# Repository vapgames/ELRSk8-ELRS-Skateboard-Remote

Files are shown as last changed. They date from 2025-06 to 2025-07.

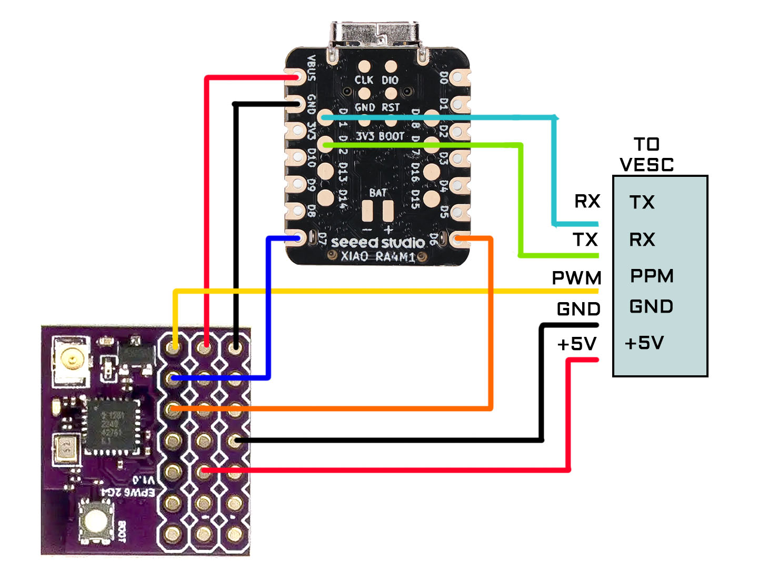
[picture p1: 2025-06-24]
schematicReceiver1.jpg

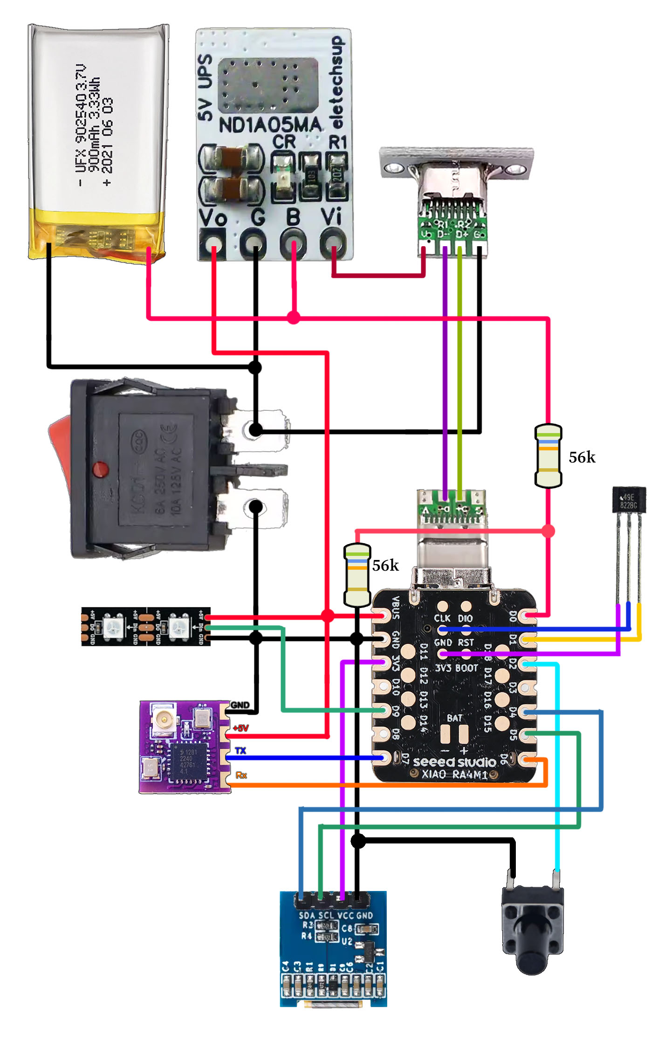
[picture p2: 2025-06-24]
schematic1.jpg

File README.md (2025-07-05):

# ELRSk8
combinedPhoto1

**This readme is under construction, more instructions and schematics are coming!**

ELRSk8 is an open source remote for DIY electric skateboard utilizing the power of [ExpressLRS](https://github.com/ExpressLRS), running on arduino-compatible controllers.

Main features I tried to achieve with this project:

1. Solve the connection and safety issue with off the shelf remotes. Low latency connection, better than NRF or BLE protocols. ELRS seems like the best open source link right now with superior interference and failsafe handling.
2. Durable throttle control with bearings, high reliability sensor and tension adjustment.
3. Ergonomic grip for use with wrist guards and gloves.
4. Basic telemetry
5. Easily sourced components, arduino compatible boards, 3d printed shell.

Code is based on ELRS control implementation from [Simple TX](https://github.com/kkbin505/Arduino-Transmitter-for-ELRS) by @kkbin505 and [AlfredoCRSF](https://github.com/AlfredoSystems/AlfredoCRSF) library by @AlfredoSystems

I've been iterating on this system for over 1 year, and I've been riding using this remote for 6 months. And at this point I'm confident enough in this design to share it.

# Remote:
<details> <summary>Remote parts you'll need (Click to expand)</summary>
  
- ExpressLRS (ELRS) - Currently it is the most reliable opensource link protocol with great interference and failsafe handling. ELRS receivers can be configured as transmitters, and there's a huge selection of different models. You can use any esp8285 based receiver for TX, I recommend "Happymodel ep1 TCXO" as TX and "Happymodel EPW6 TCXO" as RX.
  


- controller: RA4M1 it's compact and setup is straightforward. Alternatively you can use STM32F103C8T6 Blue pill (but you need to flash bootloader and remove pins to make it fit). [Xiao RA4M1](https://wiki.seeedstudio.com/getting_started_xiao_ra4m1/) OR [Waveshare RA4M1](https://www.waveshare.com/wiki/RA4M1-Zero)


- Sensor: SS49E or A1324 linear hall sensor.
  

 
- Neodimium magnets 5x3

- Bearings: MR128 ZZ (or MR128 RS)  8 * 12 * 3.5mm
  


- Spring from Bic lighter.

- Battery: 802540 or 902540 900mah li-ion spicy pillow (lasts >6 hours, haven't tested beyond that)



- Usb C port: generic pcb soldered 4 pin port.
  


- 6x6x7 button for telemetry menu
  


- Power switch: KCD1-110
  


- OLED 0.49" i2c 64x32
  


- Power supply:

    - 5v UPS module ND1A05MA - combines 0.5A charging and discharging, but seems like it's not very widely available
      
    

     - alternatively you can use 2 separate modules for charging and discharging. Look for 500ma small capacity charging module + 5v boost module
       
     

- 56k resistors x 2. For battery voltage measurement.

- Shell printed with PETG (or any other low friction material). Grips printed with TPU95a.
 
- Hardware 
  - set of m2 screws 6-12mm
    
  - m5x4 or m5x5 set screw (same as in HTD5m pulley)
    
    

- Optional WS2812 LEDs
</details>

Remote schematic for XIAO RA4M1 and ND1A05MA
schematic1



# Receiver:
- Any ELRS receiver will do. But if you want to have telemetry at this point you'll need a PWM receiver. I use Happymodel EPW6, it can do UART and PWM at the same time.

- For telemetry - to talk to VESC you need RA4M1 / STM32F103C8T6 . Or any other arduino-compatible controller that can do **2 UARTS!**

schematicReceiver1

---
# ELRS Flashing and configuring
- <details> <summary>How to enter ELRS WIFI mode (Click to expand)</summary>
  
  * For me ELRS WIFI doesn't work on my laptop, but it works on my phone.
  
  * By default ELRS receiver/transmitter will go into WIFI mode 60 seconds after power up, if there's no connection.
  
  * For fresh receiver you can power it with GND and +5v and wait 60 seconds.
  
  * If connection was established between remote and the board receiver, it will not go into WIFI mode until power cycle. So to connect WIFI to your board - keep remote turned off, power the board on, wait 60 seconds.

  * For soldered remote, the TX module will not go into WIFI mode while it's receiving packets from arduino controller. To go into WIFI mode you need to flash empty sketch (like a blinker sketch) onto the remote, then wait 60 seconds.
  
  * Choose WIFI named ExpressLRS RX (or TX). Press "Use network as is":
    
     

  * After this you can go into a browser and type address 10.0.0.1
  Here you can set your Bind Phrase, tweak pin settings, and upload the firmware (that you download from [web flasher](https://expresslrs.github.io/web-flasher/))

     
</details>

- <details> <summary>How to flash Ep1 as TX (Click to expand)</summary>
  
  * Go to https://expresslrs.github.io/web-flasher/
  
  * Choose Receiver:
  
    

  * Choose latest ELRS and these receiver settings:
  
    

  * Set your bind phrase, go to Advanced Settings and check "Flash RX as TX"
  
    

  * Download firmware and flash using WIFI method OR serial FTDI adapter
  
</details>

- <details> <summary>How to configure EPW6 for PPM and UART telemetry (Click to expand)</summary>
  
  * Go into receiver WIFI mode
    
  * CH1 is throttle PWM, I've increased mine to 100HZ, test this for your particular VESC. Make sure to setup **failsafe pos to 1500**.
    
  * CH2 and CH3 should be Serial TX and RX.
  
    

</details>

- <details> <summary>How to flash with FTDI adapter (Click to expand)</summary>
  
  * The "I wasn't asking" method that I prefer over WIFI flashing.
  
  * Bridge the boot pin or press the boot button before powering up before flashing.
  
    FTDIFlashing1

  * Use flashing method "Serial UART"
  
    

  * Select your FTDI serial in popup

    

</details>

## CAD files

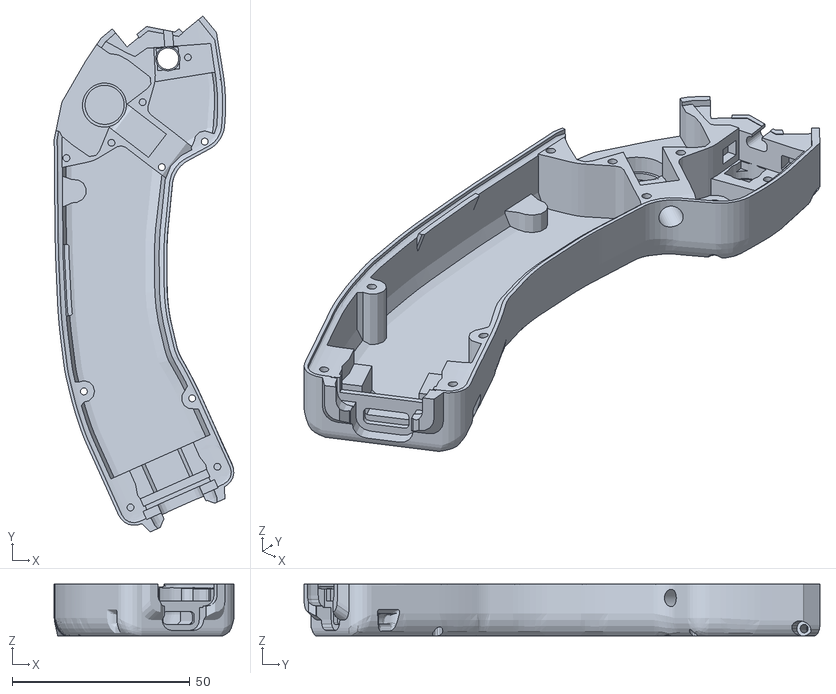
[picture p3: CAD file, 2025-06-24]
STL/remoteShellBottom.stl
50.5 x 145.0 x 14.6

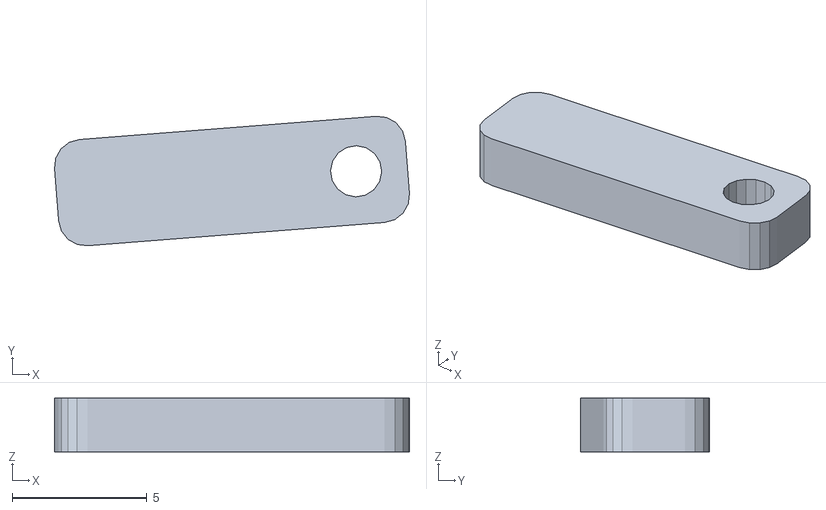
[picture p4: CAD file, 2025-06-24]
STL/buttonHolder.stl
13.2 x 4.80 x 2.00

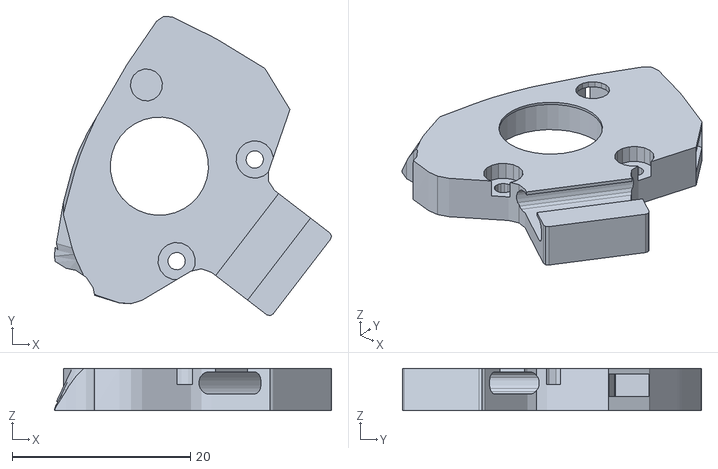
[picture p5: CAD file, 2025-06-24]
STL/gimbalLid.stl
31.0 x 33.6 x 4.71

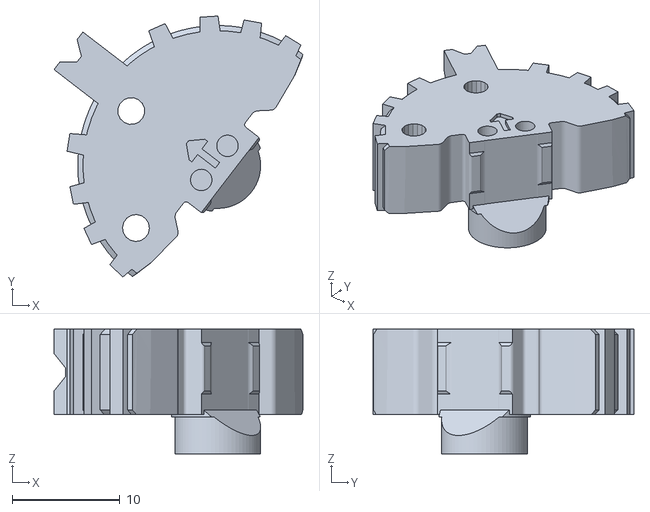
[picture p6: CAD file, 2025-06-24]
STL/knob.stl
23.1 x 24.2 x 11.6

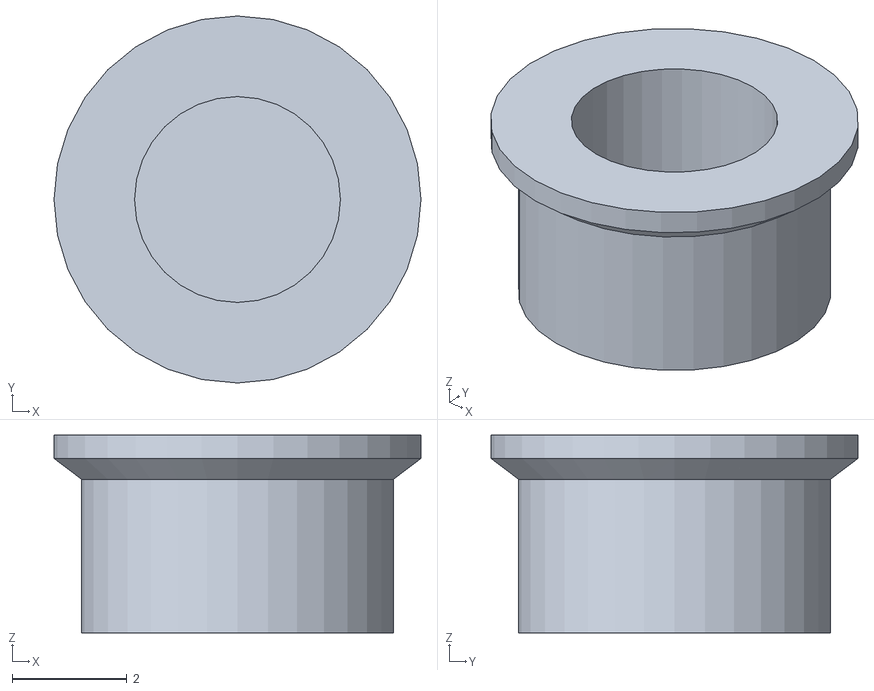
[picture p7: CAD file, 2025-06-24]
STL/buttonCap.stl
6.40 x 6.40 x 3.45

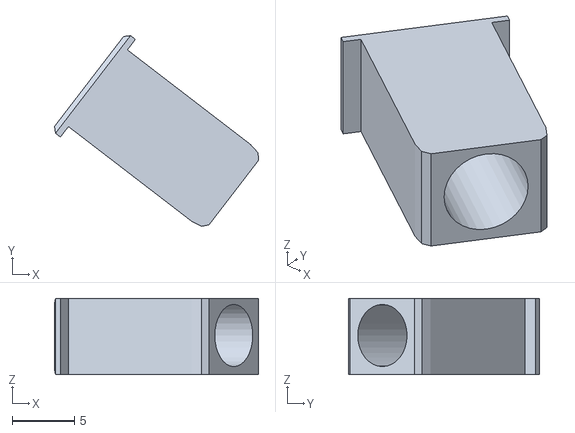
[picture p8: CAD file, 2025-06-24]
STL/plunger.stl
16.4 x 15.3 x 6.14

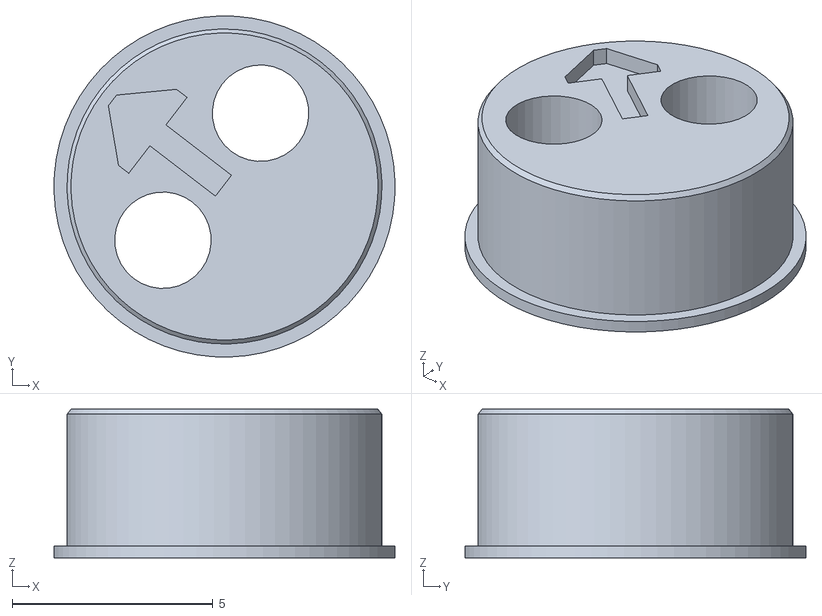
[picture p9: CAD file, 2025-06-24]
STL/axle.stl
8.49 x 8.49 x 3.70

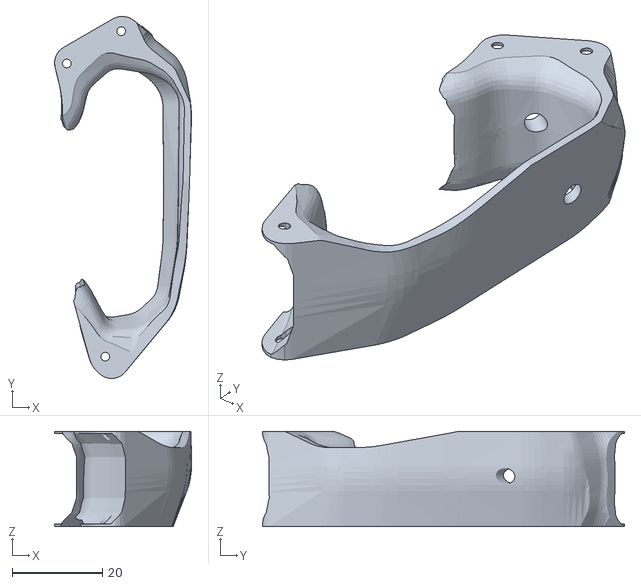
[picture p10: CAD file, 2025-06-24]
STL/grip.stl
30.4 x 80.3 x 21.2

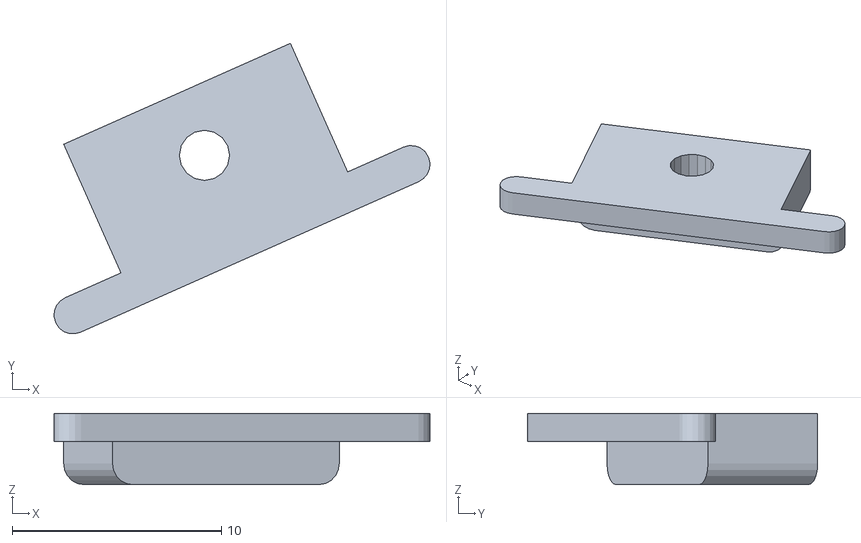
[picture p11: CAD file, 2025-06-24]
STL/usbPlug.stl
18.0 x 13.9 x 3.40

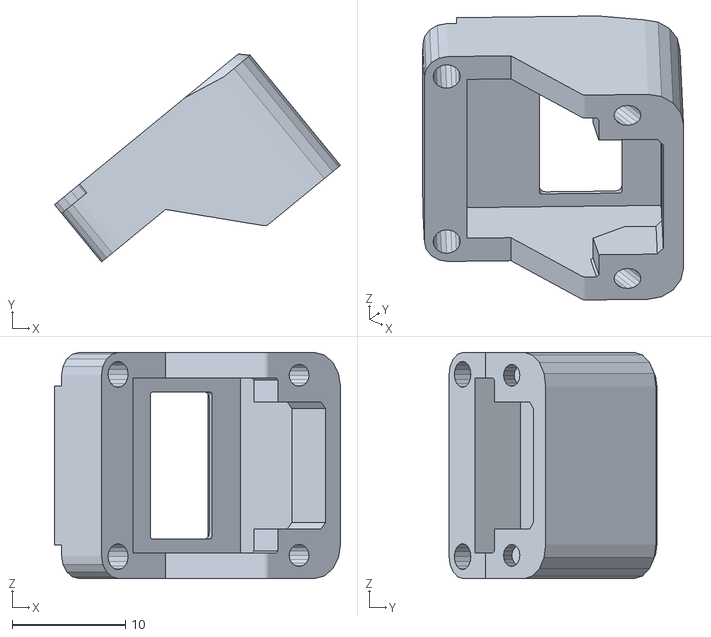
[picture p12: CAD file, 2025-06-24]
STL/oledCase.stl
25.3 x 18.4 x 20.0

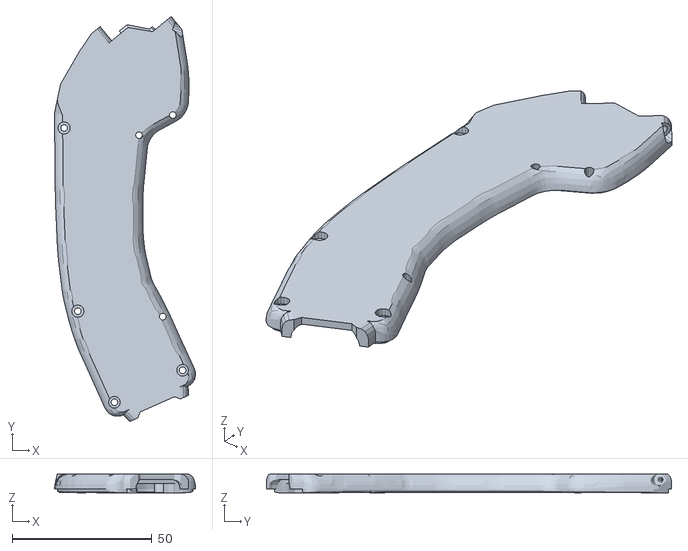
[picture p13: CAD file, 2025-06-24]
STL/remoteShellTop.stl
50.5 x 145.0 x 6.79

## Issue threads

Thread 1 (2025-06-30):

Parts

beadon, 2025-06-30:
Looking at the pictures closely, I think there are 2 (minor) additions worth mentioning in the assembly.

1. Kapton tape covering some of the connectors near the power charging section
2. Fabric(?) tape holding the throttle wires in place on one side of the remote shell.
3. padding material(?) on the inside "top" cover to pressure-mount the battery+MCU.

For someone building it without these items, it seems like the install might be a little frustrating.  Thoughts ?

Also, I think the adhesives in the fabric tape are going to break down in my relatively humid environment, so I am an advocate of some kind of "clip" or other type of cable raceway that does not require this.

beadon, 2025-07-07:
yes, that would be great.   Other people will have the same questions, I am just trying to make things easier for them.  :)

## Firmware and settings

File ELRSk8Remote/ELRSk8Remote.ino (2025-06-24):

#include <Arduino.h>
#include "crsf.h"
#include "led.h"
#include "oledScreen.h"

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
//REQUIRED LIBRARIES:
//U8x8lib
//Adafruit_NeoPixel

//CONFIG////////////////////////////

//#define CALIBRATION

//#define STM32F103C8
#define XIAOR4M1

//PINS
#ifdef STM32F103C8
  //board: generic stm32f1
  //bluepillf103c8
  //USART support: enabled (generic serial)
  //USB: CDC generic serial
  //upload method: hid bootloader 2.2
  #define CRSF_RX PB11
  #define CRSF_TX PB10
  #define OLED_SDA PB7
  #define OLED_SCL PB6
  #define VOLTAGE_READ_PIN PA6
  #define THROTTLE_PIN PA4
  #define MENU_BUTTON1_PIN PB4
  #define RGBLED_PIN PA8
  HardwareSerial CRSFSerial(CRSF_RX, CRSF_TX);
  #define CRSF_SERIAL_BAUDRATE  400000
  #define ADCResolution 12
 
  int throttleLow = 670;
  int throttleMid = 2165;
  int throttleHigh = 3650;
  
  float batteryRealVoltageLow = 3.84f;
  float batteryRealVoltageHigh = 4.2f;
  float batteryADCLow = 2341.0f;
  float batteryADCHigh = 2540.0f;
#endif

#ifdef XIAOR4M1
  #define CRSF_RX D7
  #define CRSF_TX D6
  #define OLED_SDA D4
  #define OLED_SCL D5
  #define VOLTAGE_READ_PIN A0
  #define THROTTLE_PIN A1
  #define MENU_BUTTON1_PIN A2
  #define RGBLED_PIN D9
  #define CRSFSerial Serial1
  #define CRSF_SERIAL_BAUDRATE  400000
  #define ADCResolution 14
  
  int throttleLow = 4950;
  int throttleMid = 8320;
  int throttleHigh = 11650;

  float batteryRealVoltageLow = 3.82f;
  float batteryRealVoltageHigh = 4.2f;
  float batteryADCLow = 9780.0f;
  float batteryADCHigh = 10460.0f;
#endif

int throttleSamples = 1;    //YOU CAN TRY MULTISAMPLING FOR THROTTLE INPUT IF YOU THINK IT'S TOO NOISY

int ELRSpacketRate = 3;     // 0 - 50Hz / 1 - 100Hz Full / 2- 150Hz / 3 - 250Hz / 4 - 333Hz Full / 5 - 500Hz
int ELRSpower = 0;          // 0 - 10mW / 1 - 25mW / 2 - 50mW /3 - 100mW
int ELRStelemetryRate = 4;  // 0 - Std / 1 - Off / 2 - 1:128 / 3 - 1:64 / 4 - 1:32 / 5 - 1:16 / 6 - 1:8 / 7 - 1:4 / 8 - 1:2 / 9 - Race

#define KILOMETERS
//#define MILES

//END CONFIG////////////////////////


CRSF crsf;
uint8_t crsfPacket[CRSF_PACKET_SIZE];
uint8_t crsfCmdPacket[CRSF_CMD_PACKET_SIZE];
int16_t rcChannels[CRSF_MAX_CHANNEL];
unsigned long crsfTime = 0;
unsigned long loopCount = 0;
unsigned long currentMillis = 0;
float throttle = 0;
float remoteBatteryPercent = 0;
float animationTime = 0;
OledScreenMenu oledScreen;

void setup()
{
  analogReadResolution(ADCResolution);
  pinMode(LED_BUILTIN, OUTPUT);
  pinMode(VOLTAGE_READ_PIN, INPUT);
  //TURN OFF LED TO SAVE POWER
  digitalWrite(LED_BUILTIN, HIGH); //INVERTED ON STM32f103
  
  //OLED
  int screenMode = SCREEN_VOLTAGE_DISTANCE;
  bool useKilometers = true;
  #ifdef CALIBRATION
    screenMode = SCREEN_CALIBRATION;
  #endif
  #ifdef MILES
    useKilometers = false;
  #endif
  
  oledScreen.Setup(MENU_BUTTON1_PIN, screenMode, useKilometers);
  
  //DRAW SCREEN
  for (uint8_t i = 0; i < screenTextWidth * screenTextHeight; i++) {
    oledScreen.Update();
  }

  //LED
  SetupLED(RGBLED_PIN);

  //CRSF
  //SET CHANNELS
  for (uint8_t i = 0; i < CRSF_MAX_CHANNEL; i++) {
      rcChannels[i] = (CRSF_DIGITAL_CHANNEL_MIN + CRSF_DIGITAL_CHANNEL_MAX) / 2;
  }
  //START CRSF
  delay(100);
  CRSFSerial.begin(CRSF_SERIAL_BAUDRATE);
  crsf.begin(CRSFSerial);
  crsfTime = micros();
  
  //DEBUG
  Serial.begin(115200);
  
  #ifdef CALIBRATION
    throttleMid = SampleThrottle(100);
    throttleLow = throttleMid;
    throttleHigh = throttleMid;
  #endif
}

float SampleThrottle(int samples) {
  float potInput = 0;
  for(int i = 0;i < samples;++i) {
  potInput += (float)analogRead(THROTTLE_PIN);
  }
  potInput /= samples;
  return potInput;
}

float mapfloat(float x, float in_min, float in_max, float out_min, float out_max)
{
  return constrain((x - in_min) / (in_max - in_min), 0.0f, 1.0f) * (out_max - out_min) + out_min;
}

float mapfloatUnclamped(float x, float in_min, float in_max, float out_min, float out_max)
{
  return (x - in_min) / (in_max - in_min) * (out_max - out_min) + out_min;
}

float lerp(float a, float b, float x)
{ 
  return a + x * (b - a);
}

float clamp(float x, float xMin, float xMax)
{ 
  if(x < xMin) {
    return xMin;
  }
  if(x > xMax) {
    return xMax;
  }
  return x;
}



bool CRSFUpdate() {
  unsigned long currentMicros = micros();
  //INPUT+CRSF - 635us
  if (currentMicros - crsfTime > CRSF_TIME_BETWEEN_FRAMES_US) {
    //Serial.println(currentMicros - crsfTime); //PERFORMANCE CHECK, should be close to 4000 usec
    //THROTTLE INPUT
    float potInput = SampleThrottle(throttleSamples);
    
    int CRSFThrottle = CRSFMid;
    if(potInput < throttleMid) {
      CRSFThrottle = round(mapfloat(potInput, throttleLow, throttleMid, CRSFMin, CRSFMid));
    }
    else {
      CRSFThrottle = round(mapfloat(potInput, throttleMid, throttleHigh, CRSFMid, CRSFMax));
    }

    #ifdef CALIBRATION
      rcChannels[AILERON] = CRSFMid; //DO NOT SEND THROTTLE COMMANDS DURING CALIBRATION
    #else
      rcChannels[AILERON] = CRSFThrottle;
    #endif
    
    throttle =  mapfloat(potInput, throttleLow, throttleHigh, -1.0f, 1.0f);
    

    //SEND
    if (loopCount <= 500) {
        //ESTABLISH CONNECTION BY SENDING NORMAL PACKETS
        crsf.crsfPrepareDataPacket(crsfPacket, rcChannels);
        crsf.CrsfWritePacket(crsfPacket, CRSF_PACKET_SIZE);
        loopCount++;
    } else if (loopCount > 500 && loopCount <= 505) {
        crsf.crsfPrepareCmdPacket(crsfCmdPacket, ELRS_PKT_RATE_COMMAND, ELRSpacketRate);
        crsf.CrsfWritePacket(crsfCmdPacket, CRSF_CMD_PACKET_SIZE);
        loopCount++;
    } else if (loopCount > 505 && loopCount <= 510) {
       crsf.crsfPrepareCmdPacket(crsfCmdPacket, ELRS_POWER_COMMAND, ELRSpower);
        crsf.CrsfWritePacket(crsfPacket, CRSF_PACKET_SIZE);
        loopCount++;
    } else if (loopCount > 510 && loopCount <= 515) {
        crsf.crsfPrepareCmdPacket(crsfCmdPacket, ELRS_TLM_RATIO_COMMAND, ELRStelemetryRate);
        crsf.CrsfWritePacket(crsfCmdPacket, CRSF_CMD_PACKET_SIZE);
        loopCount++;
    }
    else {
        //SEND CHANNELS
        crsf.crsfPrepareDataPacket(crsfPacket, rcChannels);
        crsf.CrsfWritePacket(crsfPacket, CRSF_PACKET_SIZE);
    }

    crsfTime = currentMicros;
    return true;
  }
  //Serial.println((micros() - currentMicros));

  return false;
}

void MeasureRemoteBattery() {
  //INTERNAL BATTERY VOLTAGE
  float batteryADC = (float)analogRead(VOLTAGE_READ_PIN);
  float batteryVoltage = mapfloatUnclamped(batteryADC, batteryADCLow, batteryADCHigh, batteryRealVoltageLow, batteryRealVoltageHigh);
  float newPercent = mapfloat(batteryVoltage, 3.2f, 4.2f, 0, 1);
  remoteBatteryPercent = lerp(remoteBatteryPercent, newPercent, 0.1f);
  oledScreen.remoteBatteryPercent = remoteBatteryPercent * 100;
}

void UpdateLed() {

  if(loopCount < 400)
  {
    //BLINK ON START
    LEDColorRGB.r = lerp(255, 0, remoteBatteryPercent);
    LEDColorRGB.g = lerp(0, 255, remoteBatteryPercent);
    LEDColorRGB.b = 0;
    blinkLED(100);
  }
  else {
    if(throttle > - 0.1f) {
      //IDLE FLASH WHITE
      animationTime += 0.01f;
      float anim = clamp(sin(animationTime) * 4 - 3, 0, 1);
      LEDColorRGB.r = lerp(0, 30, anim);
      LEDColorRGB.g = lerp(0, 40, anim);
      LEDColorRGB.b = lerp(0, 30, anim);
      
      LightLed();
    }
    else {
      //BRAKING FLASH RED
      animationTime += (0.005f - 0.015f * throttle) * 4;
      float anim = sin(animationTime) * 0.5f + 0.5f;
      LEDColorRGB.r = lerp(0, 255, anim);
      LEDColorRGB.g = 0;
      LEDColorRGB.b = 0;
      LightLed();
    }
  }

  if(animationTime > 10000.0f) {
    animationTime = 0;
  }
}

unsigned long measureMicros = micros();
int packetsPerSecond = 0;
void loop()
{
    bool crsfUpdated = CRSFUpdate();
    
    if(crsfUpdated)
    {
      ++packetsPerSecond;
      if(micros() - measureMicros > 1000000) {
        //oledScreen.distance = ((float)packetsPerSecond) * 0.1f;
        //Serial.println(packetsPerSecond);
        measureMicros = micros();
        packetsPerSecond = 0;
      }
    }
    
    
    if(!crsfUpdated) {
      //RECEIVE TELEMETRY
      crsf.handleSerialIn();
    }
    else {
      //DO SCREEN UPDATE ONCE AFTER CRSF UPDATE
      MeasureRemoteBattery();
      UpdateLed();

      //SEND TELEMETRY VALUES TO SCREEN
      oledScreen.voltage = ((float)crsf._battery.voltage) * 0.001f;
      oledScreen.distance = ((float)crsf._battery.capacity) * 0.1f;
      oledScreen.speed = ((float)crsf._battery.current) * 0.001f;
      oledScreen.current = ((float)crsf._battery.remaining) * 0.5f;
      
      //oledScreen.linkQuality = crsf._linkStatistics.uplink_Link_quality;
      //oledScreen.rssi = crsf._linkStatistics.uplink_RSSI_1;
      oledScreen.linkQuality = crsf._linkStatistics.downlink_Link_quality;
      oledScreen.rssi = crsf._linkStatistics.downlink_RSSI;
      oledScreen.Update();
    }


    #ifdef CALIBRATION
      int potInput = analogRead(THROTTLE_PIN);
      throttleLow = min(throttleLow, potInput);
      throttleMid = potInput;
      throttleHigh = max(throttleHigh, potInput);
      int calibrateVoltage = analogRead(VOLTAGE_READ_PIN);

      oledScreen.throttleCalibrate = potInput;
      oledScreen.batteryCalibrate = calibrateVoltage;
      
      Serial.println("------------------");
      Serial.print("int throttleLow = ");
      Serial.print(throttleLow);
      Serial.println(";");
      Serial.print("int throttleMid = ");
      Serial.print(throttleMid);
      Serial.println(";");
      Serial.print("int throttleHigh = ");
      Serial.print(throttleHigh);
      Serial.println(";");
      Serial.print("//battery = ");
      Serial.println(calibrateVoltage);
    #endif
}

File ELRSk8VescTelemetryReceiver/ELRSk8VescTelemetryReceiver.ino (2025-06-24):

#include <VescUart.h>
#include <SimpleKalmanFilter.h>
#include <stdio.h>
#include "crsfTelemetry.h"
#include <Arduino.h>

//REQUIRED LIBRARIES:
//VescUart
//AlfredoCRSF
//SimpleKalmanFilter

//CONFIG////////////////////////////

//#define STM32F103C8
#define XIAOR4M1

//PINS
#ifdef STM32F103C8
  #define VESC_RX PB11
  #define VESC_TX PB10
  #define CRSF_RX PA10
  #define CRSF_TX PA9
  
  HardwareSerial VESCSerial(VESC_RX, VESC_TX);
  HardwareSerial CRSFSerial(CRSF_RX, CRSF_TX);
 #endif

#ifdef XIAOR4M1
  #define VESC_RX D11
  #define VESC_TX D12
  #define CRSF_RX D7
  #define CRSF_TX D6
  
  #define VESCSerial Serial2
  #define CRSFSerial Serial1
#endif


#define KILOMETERS
//#define MILES

float numCells = 12;
float wheelDiameterMM = 102;
float motorPulleyTeeth = 15;
float wheelPulleyTeeth = 40;
int motorMagnets = 14;

//END CONFIG////////////////////////


VescUart VESCUART;
//TELEMETRY DATA
int rpm;
float voltage;
float current;
int power;
float amphour;
float tach;
float distance;
float velocity;
float watthour;
float batpercentage;
float tempEsc;
float tempMotor;
float whkm = 0;
//MAX VALUES
float maxA = 0;
float maxVel = 0;
float maxTemp = 0;
//filters
SimpleKalmanFilter cellVoltageFilter(0.01f, 0.01f, 0.01f);
SimpleKalmanFilter escTempFilter(0.1f, 0.1f, 0.1f);
SimpleKalmanFilter motorTempFilter(0.1f, 0.1f, 0.1f);


void setup() {
  Serial.begin(115200);

  //CRSF SETUP
  CRSFSerial.begin(CRSF_BAUDRATE);
  SetupCRSF(CRSFSerial);
  
  //VESC SETUP
  VESCSerial.begin(115200);
  VESCUART.setSerialPort(&VESCSerial);
}

//VESC DATA FOR REFERENCE
//struct dataPackage {
//  float avgMotorCurrent;
//  float avgInputCurrent;
//  float dutyCycleNow;
//  float rpm;
//  float inpVoltage;
//  float ampHours;
//  float ampHoursCharged;
//  float wattHours;
//  float wattHoursCharged;
//  long tachometer;
//  long tachometerAbs;
//  float tempMosfet;
//  float tempMotor;
//  float pidPos;
//  uint8_t id;
//  mc_fault_code error; 
//};


#ifdef KILOMETERS
  float metersPerMILEKM = 1.0f / 1000.0f;
#else
  float metersPerMILEKM = 1.0f / 1609.34f;
#endif
float wheelDiameterM = wheelDiameterMM / 1000.0f;
float gearingRatio = motorPulleyTeeth / wheelPulleyTeeth;

void loop()
{
  bool gotValues = VESCUART.getVescValues();

  int polePairs = motorMagnets / 2;
  rpm = VESCUART.data.rpm / polePairs;
  voltage = VESCUART.data.inpVoltage;
  current = VESCUART.data.avgInputCurrent;
  power = voltage * current;
  tempEsc = escTempFilter.updateEstimate(VESCUART.data.tempMosfet);
  tempMotor = motorTempFilter.updateEstimate(VESCUART.data.tempMotor);
  amphour = VESCUART.data.ampHours;
  watthour = VESCUART.data.wattHours;
  tach = VESCUART.data.tachometerAbs / (motorMagnets * 3);

  distance = tach * 3.14159265f * metersPerMILEKM * wheelDiameterM * gearingRatio;       // Motor RPM x Pi x (1 / meters in a mile or km) x Wheel diameter x (motor pulley / wheelpulley)
  velocity = rpm * 3.14159265f * (60.0f * metersPerMILEKM) * wheelDiameterM * gearingRatio;  // Motor RPM x Pi x (seconds in a minute / meters in a mile) x Wheel diameter x (motor pulley / wheelpulley)
  //batpercentage = (((voltage - numCells * 3.3) / numCells) + 0.04f) * 100.0f;                     // ((Battery voltage - minimum voltage) / number of cells) x 100

  maxVel = max(maxVel, velocity);
  maxTemp = max(maxTemp, velocity);
  
  float cellVoltage = cellVoltageFilter.updateEstimate(voltage / 12.0f);
  
  //SEND TELEMETRY
  crsf.update();
  sendRxBattery(cellVoltage * 100, velocity * 100, distance * 10, current * 5);
  
  delay(10);
}
